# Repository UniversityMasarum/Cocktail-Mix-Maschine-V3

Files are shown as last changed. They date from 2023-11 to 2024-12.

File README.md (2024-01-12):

# Cocktail-Maschine-V3
Eine glorreiche dritte Version der Cocktailmaschine

following https://github.com/MaxVinzens/Cocktail-Mix-Maschine-V2/tree/main there now comes the better cocktail machine. To expand skills in Git, planning as well as installation and team building under the guidance of lab engineer M.Sc. Marco Braun.

# Allgemeine Hinweise / General Notes
Cocktail-Mix-Maschine-V3 ist ein Projekt an der HTWK Leipzig im Rahmen des Moduls "Ausgewählte Themen der Automatisierungstechnik" oder "Ausgewählte Themen der Elektrotechnik". 
Im Rahmen dieses Moduls wird diese Cocktailmixmaschine realisiert, die Cocktails mischen soll und die im Vergleich zu den Version V1 und V2 einige neue Features und eine erhöhte Verlässlichkeit gewährleisten soll.

# Hardware
Als feste Voraussetzung wird verlangt, dass die Kompakt-SPS X20CP1382 von der Firma B&R verwendet wird.
Die Sensor- und Aktorenauswahl ist den Studenten freigestellt, solange diese im Rahmen des Budgets sind. Eine Eismaschine soll verwendet werden!

# Software 
Als Voraussetzung für die Realisierung wurde verlangt, die Software "AutomationStudio 4.12" von der Firma B&R zu verwenden.

# Status der Entwicklung
Komponententests und Machbarkeitsstudien

# Rules 

-Please always copy the things into a parent folder 
(C code of the PLC into the PLC folder)

-Always comment on changes

-Please do not delete old things  

-please ask if you have any questions

-for research

-don't steal my cookies

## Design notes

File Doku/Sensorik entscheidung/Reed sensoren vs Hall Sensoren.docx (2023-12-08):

Reed sensoren vs Hall Sensoren

Mögliche Systeme:

System 1 Lasersensor (TOF):

Möglicher großer Messfehler
Starke Änderungen

System 2

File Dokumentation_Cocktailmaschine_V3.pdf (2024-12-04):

## FAKULTÄT INGENIEURWISSENSCHAFTEN

### E469 - AUSGEWÄHLTE THEMEN DER AUTOMATISIERUNGSTECHNIK

# Cocktailmaschine V3

Autoren | Isabel Hansen Julien Knäbel Johannes Reitmeier Philipp Schaarschmidt Niklas Scharf Andreas Wagner Simon Wagner
Betreuer | Prof. Dr.-Ing. Jens Jäkel M.Sc. Marco Braun

### 19. September 2024

### Inhaltsverzeichnis

Tabellenverzeichnis | iv
Abbildungsverzeichnis | v
1 Bedienungsanleitung | 1
2 Betrieb | 3
3 Allgemeine Konstruktion | 11
4 Stückliste | 16
5 Energieversorgung | 16
6 Module | 20

i

ii

iii

| 6.13.2 Funktion | | 99
| 6.13.3 Betrieb | | 99

### 6.13.4 Aufbau | 100

### 6.13.5 Besonderheiten | 100

7 Programmierung der SPS | 101

### 7.1 Technische Rahmenbedingungen | 101

### 7.1.1 B&R Firma generell | 101

### 7.1.2 Verwendete Hardware-Komponenten | 102

### 7.1.3 Automation Studio | 102

### 7.1.4 Strukturierter Text | 102

### 7.1.5 Netzwerkeinstellungen | 103

### 7.2 Website | 103

### 7.2.1 B&R Website generell - MappView | 103

### 7.2.2 Praktische Umsetzung der Weboberfläche | 103

### 7.3 Hauptnavigation | 104

### 7.3.1 Reinigungsprogramm | 105

### 7.3.2 Die Auswahl für den Endnutzer | 106

### 7.3.3 Der Ladebalken | 106

### 7.3.4 Eventbindings | 107

### 7.4 Code | 107

### 7.4.1 Unterprogramme | 107

### 7.4.2 Benennung der Variablen | 108

### 7.4.3 Program - Grundlegender Ablauf | 108

### 7.4.4 Program1 - Logik zum Cocktailmixen | 112

### 7.4.5 Zufall - Zufallscocktail | 115

8 Literaturverzeichnis | 120

### Tabellenverzeichnis

1 | Stückliste Pfandsystem | | 8
2 | Stückliste Rahmen | | 11
3 | Stückliste Containerhalter | | 14
4 | Stückliste Versorgung | | 17
5 | Schaltschränke | | 18
6 | Befestigungsverfahren | | 18
| iv

7 | Spannungsebenen | | 19
8 | Stückliste Förderband | | 20
9 | Pinbelegung Förderband | | 23
10 Stückliste Getränkeschlitten | | 25
11 Funktionen der Schalter | | 28
12 Stückliste Hallsensoren | | 31
13 Pinbelegung Hallsensoren | | 34
14 Stückliste Ablaufschiene | | 34
15 Stückliste Ausschankarm | | 37
16 Stückliste Endlagenschalter | | 48
17 Stückliste Schaltpanel | | 51
18 Stückliste Becherspender | | 54
19 Stückliste Becherspender Deckel | | 63
20 Stückliste Eisspender | | 71
21 Stückliste Zitronenspender | | 79
22 Stückliste Shotspender | | 87
23 Stückliste Bestelltafel | | 99

### 24 Flussraten der Schlauchpumpen | 113

### Abbildungsverzeichnis

1 | Cocktailmaschine Vorderseite | | 3
2 | Cocktailmaschine Rückseite | | 4
3 | Cocktailmaschine von rechts | | 5
4 | Cocktailmaschine von links | | 6
5 | Schaltschrank 1 | | 7
6 | Schaltschrank 2 | | 7
7 | Testgravur | | 9
8 | Lasercutter | | 9
9 | Marke | | 9
10 Rahmen aus Aluprofilen | | 12
11 Rahmen von vorne-rechts | | 12
12 Rahmen von vorne-links | | 12
13 Grundlagen für Rahmen | | 13
14 Alurohrendkappe | | 20
15 Versorgungspanel | | 21
| v

16 Datenpanel | | 21
17 D-Sub-Terminal | | 21
18 Förderband von vorne (vor Umbau) | | 22
19 Förderband von hinten (vor Umbau) | | 22
20 Förderband von vorne (nach Umbau) | | 22
21 Förderband von hinten (nach Umbau) | | 22
22 Förderbandhalterungen und -anschlüsse | | 22
23 Getränkeschlitten mit S1 und Neodym Magnet | | 24
24 Getränkeschlitten mit Wippschalter und S3 | | 24
25 Getränkeschlitten mit S2 | | 24
26 Getränkeschlitten Seitenansicht | | 24
27 Getränkeschlitten mit geöffneter Grundplatte | | 25
28 3D-gedruckte Komponenten des Getränkeschlittens | | 26
29 Position für Gewindeeinsätze und M2,5 Muttern | | 26
30 Zuordnung der Öffnungen im Getränkeschlittengehäuse | | 27
31 Grundprogramm Getränkeschlitten | | 29
32 Unterprogramm Helligkeit und Animation | | 30
33 Hallsensor | | 32
34 Hallsensor Halterung | | 32
35 Hallsensor Halterung auf Förderband | | 32
36 Hallsensor Datenpanel M12 Stecker | | 33
37 D-Sub-Terminal | | 33
38 Ablaufschiene in Förderband | | 35
39 Ablaufschiene von der Seite | | 35
40 Ablaufschiene von oben | | 35
41 Ausschankarm in Wartestellung | | 36
42 Ausschankarm in Ausgabestellung | | 36
43 Gedruckte Komponenten des Ausschankarmes | | 38
44 Schaubild Verschraubung des Ausschankarms | | 39
45 Schnittmuster des Schwammes | | 39
46 Schaltplan Licht | | 40
47 Ansicht der Platine mit ESP | | 40
48 Ansicht der Platine ohne ESP, Spannungsteiler zu erkennen | | 40
49 Animationsrichtung | | 41
50 Grundprogramm Beleuchtung | | 42
51 Unterprogramm Helligkeit und Regenbogeneffekte | | 43

vi

52 Unterprogramm Pumpenlicht und Zufallsmodus | | 45
53 Unterprogramm Polizeifarben, Warmeiß Pulsierend, Grün, Blau | | 47
54 3D-gedruckte Komponenten des Becherspendersensor | | 49
55 3D-gedruckte Komponenten des Entnahmestationssensor | | 49
56 Sensor für die Becherregistrierung aus dem Becherspender | | 50
57 Sensor für die Registrierung der Becherentnahme | | 51
58 Schaltpanel vorne | | 53
59 Schaltpanel hinten | | 53
60 Becherspender | | 56
61 verkabelte Platine | | 57
62 Rückseite Platine | | 57
63 Hilfsplatine Relais | | 57
64 Schaltplan Becher-/Eisspender | | 58
65 Grundprogramm Becher-/Eisspender | | 59
66 Unterprogramm Becherausgabe und Eisspender SPS | | 61
67 Unterprogramm Eisausgabe Becherausgabe Knopf | | 62
68 Becherspender Deckel innerer Aufbau | | 64
69 Becherspender Deckel Außen | | 64
70 Becherspender Deckel Taster | | 65
71 Becherspender Deckel offener Deckel | | 66
72 Becherspender Deckel Alarmleuchte | | 66
73 Becherspender Deckel auf Röhre | | 67
74 Grundprogramm Beleuchtung Becherspender | | 68
75 Unterprogramm Helligkeit und Modus | | 70
76 Eiswürfelmaschine EM12E | | 72
77 Eiswürfelrutsche | | 73
78 Zusammenbau-Schema Eiswürfelrutsche | | 73
79 3D-gedruckte Befestigungsplatten | | 74
80 3D-gedruckte Unterlegscheibe | | 74
81 Laserbefestigung in Laserhaltung | | 75
82 Fotozellenbefestigung in Fotozellenhalterung | | 75
83 Abgedichtetes Loch der Fotozelle | | 75
84 Steckverbindung | | 76
85 3D-gedruckte Lichtschrankenkomponenten | | 76
86 Ausgabeknopf | | 77
87 Auslösemechanismus von vorne | | 77

vii

88 Auslösemechanismus von der Seite | | 77
89 3D-gedruckte Komponenten des Auslösemechanismus | | 78
90 Aufbau der Alu-Profile | | 80
91 Schrittmotor von hinten | | 80
92 Schrittmotorkabel | | 80
93 Ansicht mit Schrittmotor | | 80
94 Halterung des Plexiglasrohres | | 81
95 Plexiglasrohr | | 81
96 Gesamtansicht | | 81
97 Platine Zitronenspender und Ausschankarm | | 82
98 Kabelanschluss | | 82
99 Kabelanschluss Tabelle | | 82
100 Schaltplan Zitronenspender und Ausschankarm | | 83
101 Gesamter Programmablaufplan | | 84
102 Unterprogramm Zitronenspender und Schalter | | 85
103 Unterprogramm Ausschankarm und Schalter | | 86
104 Anzeige- und Displayfassung | | 88
105 Anzeige- und Displayhalterung | | 88
106 Anzeigefassung | | 89
107 Arduinohalterung | | 89
108 Ausschankarm | | 90
109 Becherhaltung | | 90
110 Servohalterung | | 91
111 Servofassung | | 91
112 Pumpenhalterung | | 92
113 Aufbau des Shotspenders | | 92
114 Grundaufbau Vierquadrantensteller | | 93
115 Programmablauf Shotspender | | 94
116 Unterprogramm Bestellvorgang | | 95
117 Messwerte der Sensoren ohne Becher | | 96
118 Messwerte der Sensoren mit Bechern | | 97
119 Shotspender-Platine | | 98
120 Menü Monitor | 100
121 Rückseite Monitor | 100
122 Aufbau vorne | 100
123 Aufbau hinten | 100

viii

124 Löcher im Profil | 101
125 Hauptnavigation | 104
126 Code Passwortabfrage | 104
127 Website Reinigungsprogramm | 105
128 Website Auswahl für den Endnutzer | 106
129 Website Ladebalken | 106
130 Website Eventbindings | 107
131 Programmablaufplan Program | 109
132 Programmablaufplan Becherspender | 109
133 Programmablaufplan Eisspender | 110
134 Programmablaufplan Zitronenspender | 111
135 Programmablaufplan Cocktailmixstation | 111
136 Programmablaufplan Becherausgabe | 112
137 Code Pumpenlaufzeiten | 113
138 TOF-Übergabeparameter | 113
139 TOF-Zeitdiagramme | 113
140 Code Flankenerzeugung Anfang | 114
141 Code Flankenerzeugung Ende | 114
142 TOF Programmcode | 114
143 Code Cocktailauswertung | 114
144 Watch Cocktailauswertung | 115
145 Programmablaufplan Zufall | 116
146 Codeausschnitt Zufallsberechungen | 116
147 Programmablaufplan Zutatenbestimmung | 117
148 Programmablaufplan Mengenbestimmung | 118
149 Programmablaufplan Ergänzen der Mengen | 119
150 Programmablaufplan Prüfen der Werte | 120

ix

## 1 Bedienungsanleitung

Vorbereitung

- Vor Inbetriebnahme auf äußere Schäden überprüfen
- Monitor ausklappen

– Monitor mithilfe von M8 Schraube am Gelenk fixieren

- Auf Verunreinigungen der Getränkebehälter und Schläuche prüfen

– Falls verunreinigt: nach Anleitung im Reinigungskonzept spülen

Eiswürfelmaschine vorbereiten:

- Stöpsel in Ablauföffnung unterhalb der Maschine stecken
- Füße der Maschine auf vorgesehene Ablagepunkte platzieren
- Seitenklappe öffnen und Wasser bis zur Markierung füllen (auf Dichtigkeit achten)
- Schutzkontaktstecker in Steckdose stecken und Maschine einschalten
- Eiswürfelgröße wählen: Größe S empfehlenswert

– Produziert neun Eiswürfel in ca. sieben Minuten
– Bei Größe L verklemmen sich Eiswürfel
- Beim Befüllen und Entleeren darauf achten, dass die Maschine immer gerade steht oder gehalten wird, da sonst Wasser austritt

Becherspenderdeckel und Becherhalter einschalten (Wippschalter):

- Helligkeit einstellen (siehe Dokumentation)
- Falls notwendig 9V-Blöcke wechseln (siehe Dokumentation)
- Sollte Becherhalter in Ausgangsposition leuchten, Reset-Knopf drücken
- Becherhalter mit Wippschalter nach rechts auf Förderband platzieren

Getränkecontainer befüllen:

- Container fest in Halterungen platzieren
- Schläuche so einführen, dass diese bis in die untere Ecke reichen
- Getränke in vorgesehene Behälter schütten (siehe Beschriftungen)
- Alle Schalter am Schaltpanel ausschalten (zeigen nach unten)
- Maschine mit Stromnetz verbinden
- Becher in Becherspender füllen
- Schalter „Becherspender öffnen“ aktivieren
- Kleinen Becherstapel von unten in Becherspender schieben, sodass oberer Rand von unterem Becher knapp über dem Greifarm liegt
- Schalter „Becherspender öffnen“ deaktivieren

1

- Becher nach und nach von oben einfüllen

Schläuche befüllen:

- Auf Touchscreen Passwort „student42“ eingeben, um Reinigungsmodus freizugeben („student“ steht schon da)
- Gefäß unter Ausschankarm stellen
- Alle Pumpen mithilfe des Reinigungsprogrammes kurz anschalten, bis aus jedem Schlauch Flüssigkeit läuft
- Passwort löschen (z.B. nur die „42“) um Reinigungsmodus zu deaktivieren

Laptop mit Bildschirm verbinden, um Menü anzuzeigen.

Betrieb

- Bestellung über Touchscreen
- Auswahl zwischen alkoholischen Getränken oder Softdrinks
- Ausgabeprozess vollautomatisch
- Getränk erst entnehmen, wenn Becher am rechten Ende angekommen ist

Funktion Schaltpanel:

- Notstop: friert Förderband und Pumpen ein
- Licht EIN / AUS: Beleuchtung der Getränkecontainer aktivieren/deaktivieren
- Modi der Beleuchtung:

– Position 1: Regenbogeneffekt
– Position 2: Pumpenlicht (aktive Pumpen beleuchtet) – Position 3: Zufallsmodus
– Position 4: Blau-Rot-Beleuchtung
– Position 5: Warmweiß pulsierend
– Position 6: Licht Grün
– Position 7: Licht Blau
- Helligkeit: in 10%-Schritten einstellbar
- Becherspender öffnen: öffnet Greifarme zum Beladen/Entladen
- Eisausgabe 1x drücken: Eisausgabezyklus
- 1x Becher: gibt einen Becher aus
- Zitronenspender EIN / AUS: aktiviert Zitronenspender
- Ausschankarm hoch / runter: Position des Arms bestimmen
- Shotspender Stromversorgung: ein/aus schalten

Becher nachfüllen:

- Wenn Rundumleuchte am Becherspender angeht

2

- Nicht überfüllen (Überlastung des Becherspenders vermeiden)

Eis nachfüllen:

- Eis in obere Klappe der Eismaschine nachfüllen
- Eismaschine kann vorher eingeschaltet werden, Eiswürfel in Gefrierbeuteln lagern

Nach der Verwendung

- Reinigung gemäß Reinigungskonzept
- Maschine von Strom trennen

## 2 Betrieb

### 2.1 Übersicht

Abbildung 1: Cocktailmaschine Vorderseite

3

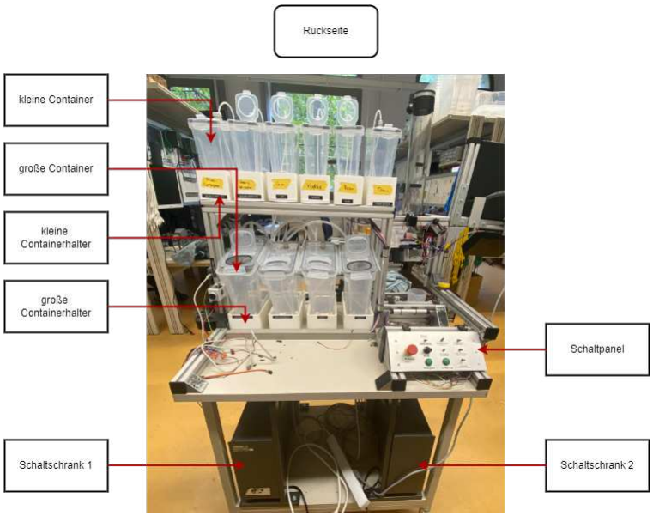
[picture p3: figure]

Abbildung 2: Cocktailmaschine Rückseite

4

Abbildung 3: Cocktailmaschine von rechts

5

Abbildung 4: Cocktailmaschine von links

6

Abbildung 5: Schaltschrank 1

Abbildung 6: Schaltschrank 2

### 2.2 Reinigungskonzept

Diese Reinigungsschritte sollen nach jeder Nutzung durchgeführt werden.

Getränkebehälter

1. Getränke aus den Behältern entfernen.
2. Topf unter Ausschankarm stellen und leeren, wenn er zu voll wird.

7

3. Mit kaltem Wasser Schläuche durchpumpen.
4. Warmes Wasser mit Spülmittel nachfüllen und Schläuche durchpumpen.
5. Danach klares Wasser hinzugeben, um restliche Spülmittelreste aus den Schläuchen zu entfernen.
6. Behälter trocknen lassen (unverschlossen).

Nach längerer Nichtnutzung der Maschine die Schläuche entfernen und reinigen.

Eismaschine

1. Restliches Wasser und Eis entfernen.
2. Eismaschine reinigen.

Zitronenspender

1. Plexiglasplatte abschrauben sowie das Plexiglasrohr aus der Halterung entnehmen.
2. Alle Plexiglasplatten sowie das Plexiglasrohr mit Spülmittel und warmem Wasser reinigen.
3. Bauteile abtrocknen.

Sonstiges

- Ablaufrinne und den Auffangbehälter leeren und reinigen.
- Förderband reinigen, falls notwendig.
- Becherhalterung reinigen, falls notwendig.

### 2.3 Pfandsystem

### 2.3.1 Stückliste

Bauteil | Anzahl
Furnier Pappel Platten 30,5x36,5cm (ges. 0,445m²) | 4

Tabelle 1: Stückliste Pfandsystem

### 2.3.2 Funktion

- Pfandmarken für Becher

### 2.3.3 Betrieb

- Bei Kauf eines Cocktails erhält Kunde zusätzlich eine Pfandmarke
- Bei Abgabe von Marke und Becher erhält der Kunde den, durch den Pfand entstandenen Aufpreis zurück

8

### 2.3.4 Aufbau

- Größe der Platten abgestimmt auf maximale Fläche des im Labor vorhandenen Lasercutters
- Logo zunächst auf die Vorderseite der Platten eingebrannt
- Platten umgedreht, Wert der Marke eingebrannt sowie ausgeschnitten

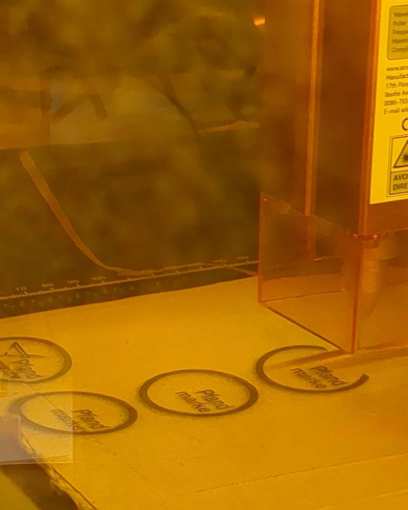
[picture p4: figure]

Abbildung 7: Testgravur

Abbildung 8: Lasercutter

### 2.3.5 Besonderheiten

Design

- Vorderseite mit Logo graviert (Oktopus)
- Rückseite spiegelt Wert der Marke wieder (zwei Euro)

Abbildung 9: Marke

9

Preisanpassung

- Preis für einen Cocktail auf drei Euro gesetzt
- Pfandmarke (zwei Euro) erhöht Gesamtpreis auf fünf Euro
- Getränk leicht mit einem Schein zu bezahlen

StuRa-Pfandsystem

- Marken bisher nicht genutzt
- Nur Veranstaltungen von Studentischer Selbstverwaltung (StuRa, FSR) begleitet
- Hier ist bereits Pfandsystem integriert, hat bisher ausreichend funktioniert

10

## 3 Allgemeine Konstruktion

### 3.1 Rahmen- und Stützstrukturen

### 3.1.1 Stückliste

Bauteil (Nutenprofil Aluminium, M8 Nut) | | Menge
Größe Querschnitt [mm] | Länge [mm] | | Bezeichnung
40x40 | 70 | 1 | Halterung Endlagenschalter
40x40 | 93 | 1 | Becherspender Längshalterung unten
40x40 | 110 | 1 | Querstrebe Eisrutsche
40x40 | 145 | 3 | Längsstreben oben
40x40 | 170 | 1 | Zitronenspender quer unten
40x40 | 200 | 1 | Zitronenspender längs oben
40x40 | 225 | 1 | Becherspender Längshalterung oben
40x40 | 230 | 1 | Zitronenspender längs unten
40x40 | 250 | 1 | Becherspender Hochkantstütze
40x40 | 295 | 1 | Querstrebe Eisservo
40x40 | 310 | 1 | Stütze Monitor hochkant
40x40 | 390 | 1 | Querstrebe Monitor
40x40 | 410 | 4 | Stützen hochkant
40x40 | 560 | 1 | Querstrebe unten
40x40 | 590 | 3 | Fundament längs auf Tisch
40x40 | 640 | 2 | Querstreben oben
40x40 | 690 | 1 | Längsstrebe Umrandung Eismaschine
40x80 | 295 | 1 | Eismaschine Fundament quer vorne
40x80 | 335 | 1 | Eismaschine Fundament quer hinten
Aluminium Profilwinkel 40x40 | | 37
Aluminium Profilwinkel 80x80 | | 6
Profilabdeckkappen 40x40 | | 15
Profilabdeckkappen 40x120 | | 3
Winkelabdeckkappen 40x40 | | 37
Winkelabdeckkappen 80x80 | | 6

Tabelle 2: Stückliste Rahmen

### 3.1.2 Funktion

Dient als generelle Struktur und Halterung vieler Baugruppen.

11

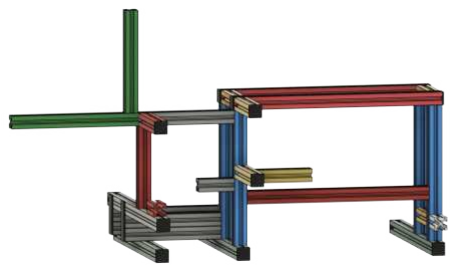
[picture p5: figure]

Abbildung 10: Rahmen aus Aluprofilen

### 3.1.3 Aufbau

- Drei Längsprofile auf Tisch montiert

– Fundament des restlichen Aufbaus
– Sehr stabile Bauteile
– Einfache aber effektive und flexible Montage durch Schraubverbindungen, Nutensteine und Profilwinkel
- Benötigt wurden Halterungen für:

– Pumpen und Schläuche
– Kleine Flüssigkeitscontainer – Ausschankarm
– Zitronenspender
– Eisrutsche
– Eismaschine
– Becherspender
– Monitor und Bestellpanel – Controlpanel
– Shotspender
– Endlagenschalter
– Kabelführungen
Abbildung 11: Rahmen von vorne-rechts | Abbildung 12: Rahmen von vorne-links

12

### 3.1.4 Besonderheiten

- Flexibles System:

– Kann wieder auseinandergebaut werden
– Leicht zu erweitern
– Mit Hilfe von 3D-Druck auf jedes Modul anpassbar

Abbildung 13: Grundlagen für Rahmen

13

### 3.2 Containerhalter

### 3.2.1 Stückliste

Bauteil | Anzahl
Großer Containerhalter | 4
Kleiner Containerhalter | 6
Plexiglasplatte 245x98x5 mm | 4
Plexiglasplatte 195x80x5 mm | 6
M8x50 Maschinenbauschrauben | 12
M8 Unterlegscheiben | 24
M8 Federringe | 12
M6x16 Maschinenbauschrauben | 24
M6 Nutensteine | 24
Kleine Peristaltikpumpe | 6
Große Peristaltikpumpe | 4
M2,5x16 Maschinenbauschraube | 12
M2,5 Mutter | 12
M3x20 Maschinenbauschrauben | 16
M3 Unterlegscheiben | 16
M3 Federringe | 16
M3 Muttern | 16
300 Ohm Resistor | 6
680 Ohm Resistor | 4
Weiße LED | 10
Lichtblende kleine Schlauchpumpe | 6
Lichtblende große Schlauchpumpe | 4

Tabelle 3: Stückliste Containerhalter

### 3.2.2 Funktion

Sowohl die großen als auch kleinen Containerhalter erfüllen die gleichen Funktionen. Mithilfe dieser lassen sich die Container fest an der Maschine montieren. Die Container werden in Schräglage befestigt, damit sämtliche Flüssigkeiten an einem Ende zusammenlaufen und vollständig herausgepumpt werden können. Durch die Schräge können die Peristaltikpumpen unterhalb der Container mithilfe des gleichen Druckes montiert werden. Zudem können LED-Panel unterhalb der Container befestigt werden, um die Getränke zu beleuchten. Am unteren Ende der Aussparung für die Pumpenmotoren befinden sich kleine Vertiefungen, durch welche LEDs durchgeführt werden können, um die Pumpen beleuchten zu können.

14

Druckanweisungen

- Kein Unterstützungsmaterial notwendig.
- Niedrige Fülldichte verwenden.
- Auf gute Bodenhaftung achten, um Verformungen zu vermeiden.
- PLA eignet sich besonders gut aufgrund guter Druckeigenschaften bei großen Drucken.

### 3.2.3 Besonderheiten

großer Containerhalter

- Bauteil zu groß für die meisten 3D-Drucker.

– Druck in zwei Teilen.

- Verkleben beider Teile nach Druck.

– UHU Hart Kunststoff gut geeignet.
– Zu flüssige Klebstoffe ziehen in Poren von 3D-Druck ein. – Beachten, dass einige Klebstoffe PLA auflösen können.

kleiner Containerhalter

- Klein genug, um auf Ender 3 in einem Stück gedruckt zu werden.

– Im Labor vorhandener Bambulab X1 Carbon könnte Probleme haben, da Kalibrierungslinien im Weg sein könnten.
– In diesem Fall Bauteil halbieren.

### 3.2.4 Montage

- Große Container mit M8 Maschinenbauschrauben an der Tischplatte verschrauben.

– Möglichst große Unterlegscheiben verwenden, um Krafteinwirkungen zu verteilen.
– Schrauben nicht zu fest anziehen.
- Kleine Containerhalter mit M6 Maschinenbauschrauben in M6 Nutensteinen im Aluprofil verschrauben.
- Kleine Peristaltikpumpen mit M2,5 Maschinenbauschrauben in kleinen Containerhaltern verschrauben.
- Große Peristaltikpumpen mit M3 Maschinenbauschrauben in großen Containerhaltern verschrauben.
- Weiße LEDs parallel zu den Pumpen schalten.

– Bei kleinen Containerhaltern LEDs 300 Ohm Widerstand vorschalten.
– Bei großen Containerhaltern LEDs 680 Ohm Widerstand vorschalten. – Siehe Stromlaufplan.
- Lichtblenden für kleine und große Pumpen anbringen.

– Bei großen Pumpen werden Blenden nur festgeklebt.

15

– Bei kleinen Pumpen müssen die unteren zwei Schrauben, welche die Glasabdeckung befestigen, entfernt und mit längeren ersetzt werden.

- Kleine Container an der langen Seite des oberen Randes mit Schaumstoffstreifen bekleben, um Container zu stabilisieren.

– Schaumstoffstreifen nicht über die gesamte Länge der oberen Kante ziehen, damit Plexiglasplatten noch eingeschoben werden können.

- Plexiglasscheiben schützen die darunter liegende Elektronik vor überlaufenden Flüssigkeiten.

## 4 Stückliste

Die Stückliste der Cocktailmaschine V3 ist aus dem folgenden Link zu entnehmen.

https://github.com/UniversityMasarum/Cocktail-Mix-Maschine-V3/blob/master/Cocktailmaschine_V3_Stückliste.pdf

## 5 Energieversorgung

Die Energieversorgung der Cocktailmaschine muss robust gegen äußere Einflüsse, optisch ansprechend und vor allem sicher für den Anwender sein. Dazu kommt noch eine möglichst schnelle und verfügbare Art und Weise des Anschlusses an Energiequellen zu gewährleisten.

16

### 5.1 Stückliste

Bauteil | Anzahl
Sperrholzplatten | 2
Siemens Schaltschrank 32x48x10cm | 2
Plexiglasscheiben Breite=45cm, Höhe=29,5 | 2
Hutschiene ca. 40cm | 2
WAGO 221-2411 Durchgangsverbinder max. 4 mm², 2 Leiter | 8
WAGO 221-412 Verbindungsklemme, 2-Leiteranschluss | 8
WAGO 221-413 Verbindungsklemme, 3-Leiteranschluss | 24
WAGO 221-415 Verbindungsklemme, 5-Leiteranschluss | 25
Befestigungsadapter WAGO 221-500 (Hutschienenadapter) | 4
UT 4 GR Universal-Terminal 0,14-4mm², grau (Reinklemme) | 1
UT 6 BL Universal-Terminal 0,2-6mm², blau (Reinklemme) | 1
UT 4 PE Universal-Terminal 0,14-4mm², grün/gelb (Reinklemme) | 1
Installationskanal CK 30x30 PVC lichtgrau ca. 60cm | 1
Verdrahtungskanal mit Deckel 25x37,5mm, 1m | 3
Verdrahtungskanal 10mm | Länge: 50cm
Alurohr Durchmesser 20mm, Wandstärke 2mm, ca.1,5m | 1
Alurohrendkappen (3D gedruckt) | 8
Kabelhalter Nut 8 | 20
Aderendhülsen 0,5mm², 1mm², 1,5mm², 2,5mm² | 70
Kabelverschraubung M20 | 1
Schutzkontaktstecker mit Kabel NYY-J 3x1,5mm², Länge: 1,8m | 1
LiYv, 0,5 mm², 25 m, rot | 1
LiYv, 0,5 mm², 25 m, blau | 1
LiYv, 0,5 mm², 25 m, grün | 1
LiYv, 0,5 mm², 25 m, violett | 1
LiYv, 0,5 mm², 25 m, orange | 1
LiYv, 0,5 mm², 25 m, weiß | 1
Cat.7 Netzwerkkabel1000 MHz S/FTP PIMF orange, ca. 8m | 1
H05V-K, 1,0 mm², blau, ca. 6m | 1
H05V-K, 1,0 mm², rot, ca. 22m | 1
H07V-K 1,5 mm² blau ca.15m | 1
H07V-K 1x1,5 grün/gelb Ring, ca. 5m | 1
H07V-K 1,5mm² grau, ca. 1,5m | 1
H07V-K 1,5 mm² orange, ca. 14m | 1
H07V-U 1x2,5 mm² violett, ca. 11m | 1
H07V-U 2,5 mm² grün/gelb ca. 0,20cm | 1
5V-Netzteil: Phoenix Contact | 1
24V-Netzteil: Phoenix Contact | 1
12V-Netzteil: omron S82K-03012 | 1

Tabelle 4: Stückliste Versorgung

### 5.2 Aufbau des Versorgungssystems

Vorbereitung für die Verkabelung der Cocktailmaschine und Schaltschränke

- Schaltschränke auf der unteren Auflagefläche montieren (z.B. Löcher in Fußgestell bohren und mit Holzschrauben fixieren)
- Kabelverschraubung in Loch im Boden des Schrank 1 anbringen
- Holzplatten zurechtschneiden und Bereich für den Schutzleiteranschluss am Schrankgehäuse

17 aussägen, anschließend mit M5 Maschinenschrauben und großen Unterlegscheiben anschrauben

- Eine Hutschiene in beide Schränke mittels Holzschrauben anbringen

Aufteilung der Komponenten in den Schränken

Schaltschrank 1 | Schaltschrank 2
Aufrasten auf Hutschiene: - Reihenklemme: Phase, Neutralleiter und Schutzleiter - WAGO-Befestigungsadapter - 5V-Netzteil - 12V-Netzteil - 24V-Netzteil Ankleben mit doppelseitigem Klebeband: - Verdrahtungskanal rechts | Aufrasten auf Hutschiene: - SPS - 2x WAGO-Befestigungsadapter - 14x Koppelrelais Ankleben mit doppelseitigem Klebeband: - Platine für Becher- und Eisspender - Platine für Zitronenspender und Ausschankarm - Beleuchtungssteuerungsplatine - Shotspendersteuerungsplatine - Verdrahtungskanal unten, rechts und oben - 3x 5er WAGO-Verbindungsklemme

Tabelle 5: Schaltschränke

- Installationskanal zusägen und auf der Oberseite der oberen Platte, hinter den unteren Getränkehaltern anschrauben.
- Verdrahtungskanal so an Unterseite der oberen Platte und an den Schränken mit doppelseitigem Klebeband fixieren, dass eine durchgehende Kanalstrecke entsteht.
- Kleiner Verdrahtungskanal hinter Aluprofil der oberen Getränkehalter kleben.
- Für Kabelverlegung entlang der Alu-Profile Alurohr mit Endkappen mittels Kabelbinder an Kabelhalter befestigen (Endkappen können 3D gedruckt werden).
- WAGO-Verbindungsklemmen mittels doppelseitigem Klebeband an Unterseite der oberen Platte für Abzweigungen vorbereiten.

Anschluss der Kabel und Verlegung

Für den Anschluss der Leiterenden, an einen Kontakt, müssen diese vom Isoliermaterial befreit werden.

Befestigungsverfahren | Hinweis
Direktes Löten | Verbindung durch Aufschmelzen von Lötzinn unter Verwendung von Flussmittel und anschließendes Erstarren (falls nötig, anschließend Schrumpfschlauch zur Isolation darüber ziehen und erwärmen)
Schraubklemme | auf abisoliertes Ende eine Aderendhülse pressen (auch bei Eingängen der SPS nötig)
WAGO-Verbindungsklemme | abisoliertes Ende wird in Klemme eingeführt

Tabelle 6: Befestigungsverfahren

18

- Stromversorgung der Maschine erfolgt über einen Schutzkontaktstecker, der in eine herkömmliche Schuko-Steckdose (230 V, Typ F) eingesteckt wird (Die Eismaschine und der Monitor für die Getränkekarte müssen separat über einen Schukostecker an eine Schukosteckdose des Typs F angeschlossen werden).
- Kabel des Schuko-Steckers durch die Unterseite in den Schrank 1 führen, dort mittels Kabelverschraubung zugentlasten und an die Reihenklemmen für Phase, Neutralleiter und Schutzleiter anschließen.
- Von Reihenklemmen mittels H07V-K Brücken zu WAGO-Klemmen und anschließend zu den 5V-, 12V- und 24V-Netzteilen.
- Grün-gelber Schutzleiter mit dem Gehäuse von Schrank 1 und Schrank 2 sowie mit dem WAGO-Switch 852-111 und dem Förderband verbinden.

Spannungsebenen und die dazugehörigen Verbraucher

5V | 12V | 24V
- Platine für Becher- und Eisspender | - kleine Peristaltikpumpen und | - speicherprogrammierbare Steuerung
- Platine für Zitronenspender | parallel geschaltene Widerstände | - große Peristaltikpumpen und parallel
und Ausschankarm | und Leuchtdioden | geschaltene Widerstände und Leuchtdioden
- Beleuchtungssteuerungsplatine | - Schrittmotor des Zitronen- | - WAGO-Switch 852-111
- Shotspendersteuerungsplatine | spenders | - B&R Touchscreen
- Servomotoren in Becherspender,
Eisspender, Ausschankarm und
Shotspender
- fokussierbares Lasermodul
- Beleuchtung der Getränke und der Shotgläser

Tabelle 7: Spannungsebenen

Hinweis: Der Maximalbetrieb der RGB-LED-Panels für die Getränkebehälter ist nicht möglich, da dies das 5V-Netzteil überlasten würde. Um dies zu verhindern, werden Helligkeitsanpassungen und geeignete Lichteffekte eingesetzt, bei denen nicht immer alle Leuchtdioden gleichzeitig weißes Licht abstrahlen. Dies wird softwaretechnisch realisiert.

Die Masse der 5-V-Spannungsebene ist separat zur zusammengefassten Masse der 12-V- und 24-V-Spannungsebene geführt, um „zitternde“ Servomotoren und flackernde Lichter zu vermeiden.

- Weitere Informationen zur Verkabelung können dem Stromlaufplan entnommen werden.

Auswahl des Leiterquerschnittes:

- Querschnitt der Kupferleiter für die Komponentenversorgung beträgt mindestens 1 mm² und ist damit mit bis zu 15 A belastbar (Die höchste Stromstärke im Normalbetrieb wird mit 6,5 A in der Versorgungsleitung der Getränkebehälterbeleuchtung erwartet).
- Signalübertragungsverbindungen haben einen Leiterquerschnitt von 0,5 mm² oder bestehen aus Aderpaaren eines CAT-7-Netzwerkkabels, das durch geerdete Schirmung eine störungsfreie Signalübertragung ermöglicht.

19

Schutzvorrichtungen:

- Alle selbst entwickelten Module der Cocktailmaschine arbeiten mit Sicherheitskleinspannung
- Zum Schutz vor Berührung, Fremdkörpern und Flüssigkeiten sind die Schränke durch angeschraubte Plexiglasscheiben abgeschirmt
- Kabelkanäle und Alurohre schützen die Kabel

Informationen zu der Alurohrendkappe:

- Material: PLA
- Kein Unterstützungsmaterial nötig
- Nutzen: Schützt Leiter vor scharfen Kanten am Alurohr

Abbildung 14: Alurohrendkappe

## 6 Module

### 6.1 Förderband

### 6.1.1 Stückliste

Bauteil | Anzahl
Transfersystem 24V DC | 1
D-Sub 25-Kabel | 1
Bananenstecker | 3

Tabelle 8: Stückliste Förderband

### 6.1.2 Funktion

- Transfer des Bechers zwischen den einzelnen Stationen

20

### 6.1.3 Betrieb

- Motor innerhalb des Förderbandes ist über Achse mit zwei Bändern verbunden
- Im Betrieb benötigt Motor 24V / 1,1A
- Drehrichtung kann über entsprechende Pin-Ansteuerung geändert werden

### 6.1.4 Aufbau

- Am Rahmen sind zwei Panele angebracht

– Versorgungspanel mit Bananenbuchsen
– Datenpanel mit acht M12-Buchsen und einer D-Sub 25-Buchse
Abbildung 15: Versorgungspanel | Abbildung 16: Datenpanel
- Pinbelegung von Datenpanel und Versorgungspanel intern verschalten
- Nach ausgiebiger Durchgangsprüfung Pinbelegung festgestellt
- Möglichkeit des Austausches zwischen Links- und Rechtslauf des Förderbandes sowie sechs externer Geräte und SPS über D-Sub 25-Anschluss

Abbildung 17: D-Sub-Terminal

21

- Anschluss der Betriebsspannung mit 24V, Masse und PE über Bananenstecker am Versorgungspanel
- Für Nutzung der Richtungssteuerung per D-Sub 25-Anschluss muss der Schalter “SPEED CTRL. INT.” auf INT. (intern) gestellt werden

Abbildung 18: Förderband von vorne (vor Umbau)

Abbildung 19: Förderband von hinten (vor Umbau)

### 6.1.5 Besonderheiten

Umbau Förderband

- Förderband besitzt zwei Panele (Versorgungspanel, Datenpanel)
- Jeweils eines der beiden auf einer Seite
- Umbau so, dass beide Panele auf einer Seite sind
- Vorteile:
– Unbefugte Personen kommen nicht an Schaltungen
– Schaltung nicht von außen zu sehen
– Kürzere und unumständlichere Verkabelung zwischen Förderband, Sensorik und SPS

Abbildung 20: Förderband von vorne (nach Umbau)

Abbildung 21: Förderband von hinten (nach Umbau)

Halterung

- Sechs kleine Halterungen an Tischplatte unter Förderband angeschraubt
- Füße des Förderbandes können dort hineingestellt werden
- Kein Verrutschen des Förderbandes möglich

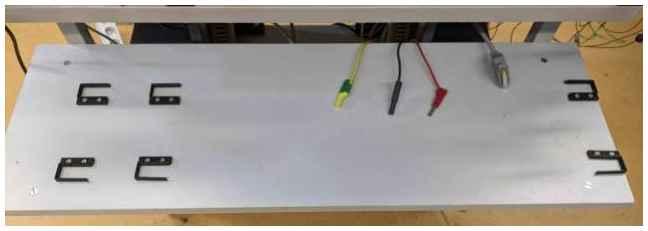
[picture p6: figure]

Abbildung 22: Förderbandhalterungen und -anschlüsse

22

Pinbelegung

D-Sub 25 Pin | M12 Pin | Bezeichnung/Belegung
1 | X5 1.4 | nicht verwendet
2 | X5 2.1 | nicht verwendet
3 | X5 3.4 | nicht verwendet
4 | X5 4.1 | nicht verwendet
5 | X5 5.4 | nicht verwendet
6 | X5 6.1 | nicht verwendet
7 | X5 7.4 | Band Rechtslauf
8 | X5 8.1 | Band Linkslauf
9 | - | nicht verwendet
10 | X5 1.1 / 2.2 / 3.1 / 4.2 / 5.1 / 6.2 / 7.1 / 8.2 | Spannungsversorgung 24V
11 | - | keine interne Verschaltung
12 | - | keine interne Verschaltung
13 | X5 1.3 / 2.4 / 3.3 / 4.4 / 5.3 / 6.4 / 7.3 / 8.4 | Masse 1
14 | X5 1.2 | Datenpin Hallsensor 1
15 | X5 2.3 | Datenpin Hallsensor 2
16 | X5 3.2 | Datenpin Hallsensor 3
17 | X5 4.3 | Datenpin Hallsensor 4
18 | X5 5.2 | Datenpin Hallsensor 5
19 | X5 6.3 | nicht verwendet
20 | X5 7.2 | Reserve Band Linkslauf
21 | X5 8.3 | Reserve Band Linkslauf
22 | - | nicht verwendet
23 | X5 1.1 / 2.2 / 3.1 / 4.2 / 5.1 / 6.2 / 7.1 / 8.2 | Intern mit Pin 10 gebrückt
24 | - | nicht verwendet
25 | X5 1.3 / 2.4 / 3.3 / 4.4 / 5.3 / 6.4 / 7.3 / 8.4 | Masse 2

Tabelle 9: Pinbelegung Förderband

### 6.2 Getränkeschlitten

Der Getränkeschlitten hat die Aufgabe einen Becher zuverlässig aus dem Becherspender aufzunehmen, diesen sicher zu den einzelnen Stationen entlang des Förderbandes zu transportieren und eine leichte Entnahme durch den Kunden zu ermöglichen. Ebenso soll der Getränkeschlitten entlang des Förderbandes für die SPS lokalisierbar sein und selbst den Fortschritt der Cocktailherstellung registrieren.

23

Abbildung 23: Getränkeschlitten mit S1 und Neodym Magnet

Abbildung 24: Getränkeschlitten mit Wippschalter und S3

Abbildung 25: Getränkeschlitten mit S2 | Abbildung 26: Getränkeschlitten Seitenansicht

24

Abbildung 27: Getränkeschlitten mit geöffneter Grundplatte

### 6.2.1 Stückliste

Bauteil | Anzahl
Neodym Magnet (D=7mm/ Höhe=3mm) | 1
Mikro Rollhebelschalter | 1
Wippschalter 1802 | 1
Kurzhubtaster | 2
Plexiglasscheibe (Durchmesser=60mm/ Höhe=3mm) | 1
Arduino Nano | 1
LED-Ring RGB WS2812B | 1
Lochplatine (Länge=70mm/ Breite=20mm) | 1
Widerstand R= 10kΩ | 3
9V Block | 1
9V Block Batterieclip | 1
M3x6 Maschinenschrauben | 4
M3x12 Maschinenschrauben + Unterlegscheibe | 4
M3x5,7 Gewindeeinsatz | 8
M2,5x10 Maschinenschrauben + Unterlegscheibe | 2
M2,5 Mutter | 2
LiYv 1x0,5mm² blau (ca. 50cm) | 1
LiYv 1x0,5mm² rot (ca. 50cm) | 1
LiYv 1x0,5mm² orange (ca. 10cm) | 1
Buchsenleiste (15 Buchsen) | 2

Tabelle 10: Stückliste Getränkeschlitten

### 6.2.2 Druckanweisung

- mit Unterstützungsmaterial
- keine hohe Fülldichte nötig
- Material: PLA

25

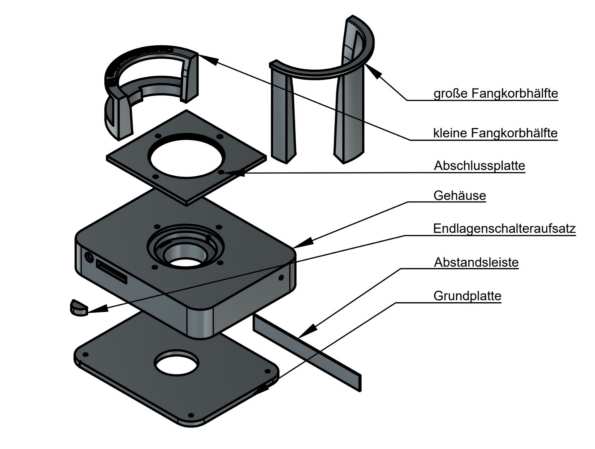
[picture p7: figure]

Abbildung 28: 3D-gedruckte Komponenten des Getränkeschlittens

### 6.2.3 Zusammenbau der einzelnen Komponenten

- 3D gedruckte Teile vom Unterstützungsmaterial befreien

Abbildung 29: Position für Gewindeeinsätze und M2,5 Muttern

- Gewindeeinsätze mittels Gasbrenner erhitzen und mit einer geeigneten Zange in die angegebenen Löcher drücken (schmelzen)
- M2,5 Mutter mit einem stumpfen Gegenstand (Holzstiel eines Hammers) in die Vertiefung pressen
- an Taster- und Wippschalterkontakte Leiter (LiYv) löten, anschließend in vorgesehene Öffnungen schieben und mit Heißkleber von innen fixieren
- Leiter an Rollhebelschalter anlöten (wird als Schließer verwendet)

26

- Endlagenschalteraufsatz auf Schalterarm drücken und mit Sekundenkleber sichern (dieser ermöglicht die beidseitige Betätigung beim Links- und Rechtslauf des Förderbandes)
- Rollhebelschalter mittels M2,5x10 Maschinenschrauben und Unterlegscheiben fixieren

Abbildung 30: Zuordnung der Öffnungen im Getränkeschlittengehäuse

- Neodym Magnet mit einem stumpfen Gegenstand in Öffnung pressen
- LED-Ring von Oberseite so einschieben, dass Kontakte durch die Anschlussöffnung frei zugänglich sind und Leiter anlöten
- auf Lochplatine Buchsenleisten in Passgröße des Arduino Nano, sowie 10kΩ- Pulldown-Widerstände anlöten
- 9V Block Batterieclip, sowie Leiter der Schalter und Taster an Platine anlöten und nach Schaltplan verschalten (siehe „Schaltplan_Becherhalter“) Hinweis: vor Inbetriebnahme Leiterbahnen auf der Platine durchmessen, um Kurschlüsse zu vermeiden
- Programm „Becherhalterbeleuchtung“ auf Arduino laden
- 9V Block in Käfig einschieben und mit Batterieclip verbinden
- Plexiglasscheibe über den LED-Ring einlegen, darüber die Abschlussplatte so positionieren, dass von der Unterseite des Gehäuses, die M3x12 Schrauben, mit Unterlegscheibe, durch die Löcher gefädelt und mit den Fangkorbhälften verschraubt werden kann (dabei werden Abschlussplatte und Plexiglasscheibe verklemmt und fixiert)
- Für Feuchtigkeitsschutz alle Kanten auf der Gehäuseoberseite mittels Heißklebernaht abdichten
- Grundplatte mittels M3x6 Maschinenschrauben mit Gehäuse verschrauben

### 6.2.4 Allgemeine Erläuterung

Positionsübermittlung des Becherhalters an die SPS

Entlang des Förderbandes befinden sich Hallsensoren, welche das vom verbauten Neodym Magneten erzeugte Magnetfeld registrieren und ein Signal an die SPS schicken.

Positionserkennung des Becherhalters

Beim Vorbeifahren des Becherhalters an den Hallsensoren wird der Endlagenschalter betätigt. Jede Betätigung wird vom Arduino erfasst und gezählt, sodass passend zur Station ein Lichteffekt wiedergegeben werden kann. Nachdem der Becherspender an der Getränkeausgabe angekommen ist, wird

27 das Licht auf dem Rückweg ausgeschaltet. Dies verlängert die Lebensdauer der Batterie. Weitere Informationen können dem Programmablaufplan entnommen werden.

Hinweis: Der Becherhalter muss an der Ausgangsposition, an dem Becherspender eingeschalten, oder zurückgesetzt werden. Andernfalls kommen nicht die gewünschten Lichtanimationen an den jeweiligen Stationen.

Batterielaufzeit

Der maximale Strombedarf der Schaltung liegt bei 46mA (Helligkeitseinstellung → alle LEDs sind weiß).

Batterielaufzeit bei einem 9V-Block mit 640mAh*:

Batterielaufzeit t = Kapazität 9V-Block / max. Strombedarf = 640mAh/46mA = 13,9h

Im Ruhemodus hat die Schaltung einen Strombedarf von 21 mA. (Diese Werte wurden messtechnisch mit einem Digital-Multimeter VC-125 ermittelt.)
Der Wippschalter unterbricht den Stromkreis zur Batterie. Dies verhindert eine schnelle Entladung der
Batterie bei Nichtnutzung.

*https://www.varta-ag.com/fileadmin/varta/industry/images/products/Industrial_Pro/VM_Folder_Industrial_Pro_2023_Web.pdf

Hinweis zum Stromlaufplan

Schaltobjekt | Pin | Funktion
Rollhebelschalter (S1) | D03 | Stationserkennung
Taster (S2) | D03 | Zurücksetzen
Taster (S3) neben dem Wippschalter | D04 | Helligkeitseinstellung

Tabelle 11: Funktionen der Schalter

### 6.2.5 Programmablauf

Grundprogramm

- LEDs ausschalten, um vorherige Zustände zu löschen
- Auf Inputs warten

– Knopf „Helligkeit“ gedrückt
– Taster „Station“ betätigt
– Knopf „Reset“ gedrückt

Taster „Station“ betätigt

- Dieser Taster befindet sich an der Seite des Becherhalters und wird während der Fahrt betätigt, indem dieser gegen die Hallsensoren drückt

– Becherhalter kennt die Station, an der er sich befindet

- Variable counterStation zählt mit, an welcher Station der Becherhalter sich befindet

– Hin und zurück sind 7 Klicks

- Aktionen bei Werten von counterStation:

28

– 1: LEDs aus → Startposition, es wird Energie gespart, wenn Becherhalter nicht in Benutzung
– 2: LED Animation Blau
– 3: LED Animation Gelb
– 4: LED Animation Magenta
– 5 – 7: LED Animation Rot (Becherhalter ist auf dem Rückweg), wenn an Startposition angekommen, counterStation = 1 → LEDs aus

Knopf „Reset“ gedrückt

- Setzt Variable counterStation auf 1, um Programm von vorne beginnen zu lassen

Abbildung 31: Grundprogramm Getränkeschlitten

Unterprogramm Animation

- for-Schleife von i = 0 bis i < 12 laufen lassen

– LED(i) auf Farbe der Station schalten
– Pause von Animationsdauer / 12 (Anzahl LEDs auf LED-Ring)

29

Unterprogramm Helligkeit

- Variable count zählt die Anzahl der Tastendrücke
- 6 Helligkeitsstufen

– Helligkeit berechnet mit Formel: Helligkeit = 255 / 6 * count

- LED-Ring füllt sich mit zunehmender Helligkeit

– Berechnet mit Formel: LEDs an = 2 * count

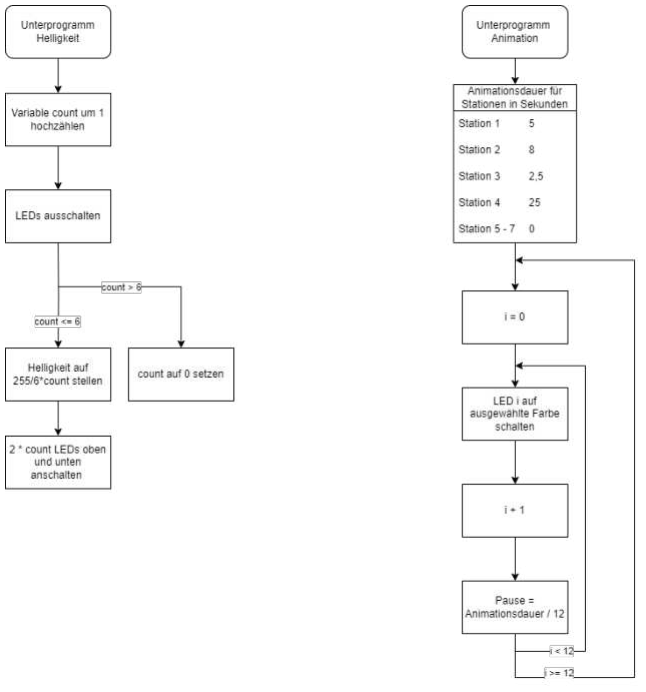
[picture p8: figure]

Abbildung 32: Unterprogramm Helligkeit und Animation

30

### 6.3 Hallsensoren

### 6.3.1 Stückliste

Bauteil | Anzahl
Hallsensor | 5
Halterung Hallsensor | 5
M12 Stecker gewinkelt | 5
D-Sub 25 Terminalblock | 1
Aderendhülsen 0,5 mm² | 15
M3x25 Maschinenbauschraube | 10
M3x10 Maschinenbauschraube | 6
M3 Unterlegscheibe | 14
M3 Mutter | 10
M3 Nutenstein | 6
M4x10 Maschinenbauschraube | 4
M4 Unterlegscheibe | 4
M4 Nutenstein | 4
Kabelkanal | 50cm

Tabelle 12: Stückliste Hallsensoren

### 6.3.2 Funktion

Feststellung der Position des Schlittens und Festlegung der Stationen.

### 6.3.3 Betrieb

- Sensorkopf detektiert Magnetfelder in kleinem Bereich vor ihm
- Im Betrieb benötigt der Sensor 24V / 0,2A
- Schlitten für Transport des Bechers beinhaltet im Gehäuse einen kleinen Neodym Magneten

– Sensor erkennt Magneten und gibt HIGH-Signal an SPS
– SPS hält daraufhin Förderband an und löst Ablauf der entsprechenden Station aus

### 6.3.4 Aufbau

- Fünf Hallsensoren einzeln auf dem Rahmen des Förderbandes montiert

– Jeder Sensor dient einer Station:
* Startposition und Becherausgabe * Ausgabe Eis
* Ausgabe Zitrone
* Ausgabe Getränke

31

* Endposition

- Halterung auf Förderband über 3D-Druck realisiert und mit Nutensteinen und Schraubverbindung befestigt
- Abstand zum Schlitten kann durch Schraubverbindung im geringen Maß angepasst werden
Abbildung 33: Hallsensor | Abbildung 34: Hallsensor Halterung

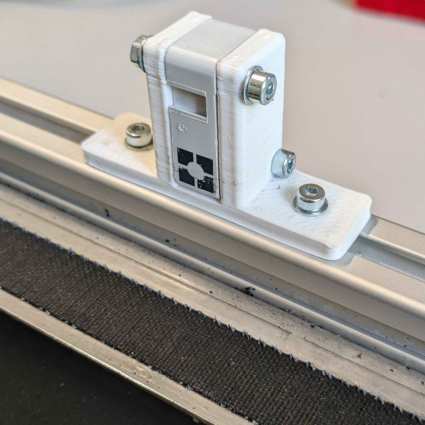
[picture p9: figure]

Abbildung 35: Hallsensor Halterung auf Förderband

### 6.3.5 Besonderheiten

Verkabelung über Förderband

- Jeder Sensor verfügt über drei Anschlussleitungen (Spannung, Masse, Datenausgang)
- Sowohl Spannungsversorgung als auch Datenausgänge können über Ein- und Ausgänge des Förderbands mit SPS verbunden werden

32

– Sensoren sind über M12-Stecker an das Förderband angeschlossen
– Spannungsversorgung und Kommunikation mit SPS erfolgt über D-Sub 25-Kabel
– Geringer Verkabelungsaufwand, da D-Sub 25-Kabel ebenfalls für die Steuerung des Förderbands dient
- D-Sub 25-Kabel wird an Terminal angeschlossen

Abbildung 36: Hallsensor Datenpanel M12 Stecker

Abbildung 37: D-Sub-Terminal

33

Pinbelegung

D-Sub 25 Pin | M12 Pin | Bezeichnung / Belegung
10 | X5 1.1 / 2.2 / 3.1 / 4.2 / 5.1 / 6.2 / 7.1 / 8.2 | Spannungsversorgung 24V
13 | X5 1.3 / 2.4 / 3.3 / 4.4 / 5.3 / 6.4 / 7.3 / 8.4 | Masse 1
14 | X5 1.2 | Datenpin Hallsensor 1
15 | X5 2.3 | Datenpin Hallsensor 2
16 | X5 3.2 | Datenpin Hallsensor 3
17 | X5 4.3 | Datenpin Hallsensor 4
18 | X5 5.2 | Datenpin Hallsensor 5

Tabelle 13: Pinbelegung Hallsensoren

### 6.4 Ablaufschiene

### 6.4.1 Stückliste

Bauteil | Anzahl
Aluminiumblech 60x11cm | 1
Profilwinkel 20x20mm | 5
M5x8 Maschinenbauschraube | 5
M5 Nutenstein | 5

Tabelle 14: Stückliste Ablaufschiene

### 6.4.2 Funktion

Schutz der Bauteile vor Getränkeüberresten / umgeschütteten Flüssigkeiten.

### 6.4.3 Betrieb

- Getränkereste in Schläuchen tropfen gelegentlich von Arm auf Förderband oder dazwischen
- Blech fängt diese zu großen Teilen ab
- Kann in Sammelschale abgeführt werden

### 6.4.4 Aufbau

- Alu-Blech leicht gewölbt und Kanten nach oben geknickt
- Ohne weiteren Schutz sammelt sich viel Rost auf Blech
- Mit schwarzer Sprühfarbe eingefärbt
- Mit Papier abgedeckt und ausgeschnittenen Schriftzug weiß angesprüht

34

- Für langen Halt der Farben dreimal mit Klarlack übersprüht
- Über 20x20 mm Profile innerhalb des Förderbandes eingeklemmt
- Klemmt genau so, dass keine Förderbandrolle am Blech schleift

Abbildung 38: Ablaufschiene in Förderband

Abbildung 39: Ablaufschiene von der Seite

### 6.4.5 Besonderheiten

- Schriftzug wurde mit Lasercutter in Papier geschnitten
- Stellt „Cocktailmaschine V3“ dar, da dritte Version der Maschine

Abbildung 40: Ablaufschiene von oben

### 6.5 Ausschankarm

Der Ausschankarm dient der spritzminimierten Ausgabe der Getränke, indem er mittels Absenkens der Ausgabeöffnungen den Abstand zwischen Becherrand und Getränkeausgabeelement verringert. Zusätzlich soll er die, zwischen den Ausgaben, austretenden Flüssigkeiten zuverlässig sammeln, um eine Verschmutzung der restlichen Maschine zu verhindern.

35

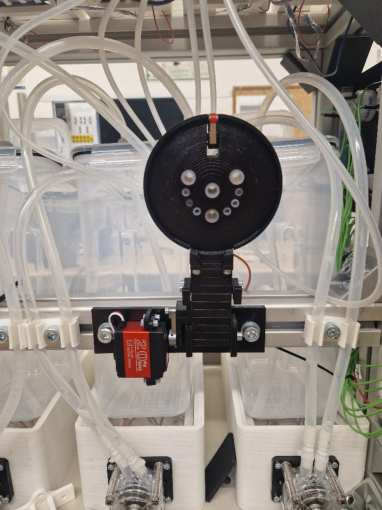
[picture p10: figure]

Abbildung 41: Ausschankarm in Wartestellung Abbildung 42: Ausschankarm in Ausgabestellung

36

### 6.5.1 Stückliste

Bauteil | Anzahl
Nutenstein P40 M8 | 2
M2,5x10 Maschinenschraube | 1
M2,5 Mutter | 1
M2,7 Unterlegscheibe | 1
M3x10 Maschinenschraube | 9
M3x16 Maschinenschraube | 2
M3,2 Unterlegscheibe | 15
M3 Federring | 1
M3x5,7 Gewindeeinsatz | 11
M4x6 Maschinenschraube | 1
M4x40 Maschinenschraube | 1
M4,3 Unterlegscheibe | 1
M4 Mutter | 1
M8x16 Maschinenschraube | 2
M8,4 Unterlegscheibe | 2
Servomotor DS3218 | 1
Micro Rollen Hebel Schalter | 1
Widerstand 11kΩ | 1
LiYv 1x0,5mm² orange (ca. 20cm) | 1
LiYv 1x0,5mm² weiß (ca. 20cm) | 1
Buchsenleiste 2,45mm (5 Buchsen) | 1
Stiftleiste 2,45mm (5 Anschlüsse) | 1
Schrumpfschlauch ca. 2cm | 7
Druckfeder aus Kuli | 1
Reinigungsschwamm | 1

Tabelle 15: Stückliste Ausschankarm

### 6.5.2 Druckanweisung

- mit Unterstützungsmaterial
- keine hohe Fülldichte
- Material: PETG

37

Abbildung 43: Gedruckte Komponenten des Ausschankarmes

### 6.5.3 Zusammenbau der einzelnen Komponenten

- Unterstützungsmaterial aus der Vertiefung am Ausschankkopf und allen Löchern entfernen
- M3x5,7 Gewindeeinsatz mit Gasbrennerflamme erwärmen und in gekennzeichnete Löcher drücken
- alle 3D gedruckten Teile nach nachfolgendem Bild verschrauben
- Leiter an Rollhebelschalterkontakte löten (wird als Schließer genutzt) und mittels Schrumpfschlauch überdecken (auch hinteren freien Kontakt mit Schrumpfschlauch versehen)
- Rollhebelschalter am Ausschankkopf so befestigen, dass dieser sich um die Verschraubung drehen kann
- Druckfeder auf das Gewinde der M4x6 Maschinenschraube aufdrehen und die Feder mittels Seidenschneider so kürzen, dass der Rollhebelschalterarm unterhalb der Unterkannte des Ausschankkopfs gedrückt wird
- Druckfeder über hinteren, mit Schrumpfschlauch abgeschirmten, Kontakt stecken
- Servomotor mit mitgelieferten Servoarm verschrauben, anschließend an Befestigungsplatte verschrauben
- Servoarm mit Arm verschrauben (Beachtung des Drehbereiches des Servomotors erforderlich!)
- Nutensteine in Aluprofil klemmen, und Befestigungsplatte anschrauben
- Verbindung zwischen Versorgung / Steuerplatine mittels Buchsenleiste und Stiftleiste herstellen

– Verdrahtung kann dem Stromlaufplan entnommen werden

- Schläuche werden zuerst durch die Zugentlastung und dann in Löcher des Ausschankarmes geschoben

38

Abbildung 44: Schaubild Verschraubung des Ausschankarms

### 6.5.4 Schnittmuster des Schwammes

Abbildung 45: Schnittmuster des Schwammes

Da die Schwammhalterungen den Schwamm auch ohne einen extra Zuschnitt fixieren können, ist dieser nicht zwingend notwendig.

### 6.5.5 Allgemeine Erläuterungen

Die Zugentlastung soll verhindern, dass durch die Auf- und Abwärtsbewegung des Ausschankarmes die Schläuche aus den Löchern im Ausschankkopf rutschen. Besonders im Moment des Tropfen-Abschüttelns ist diese zusätzliche Befestigung von großer Bedeutung.

39

### 6.6 Beleuchtung

### 6.6.1 Schaltplan Licht

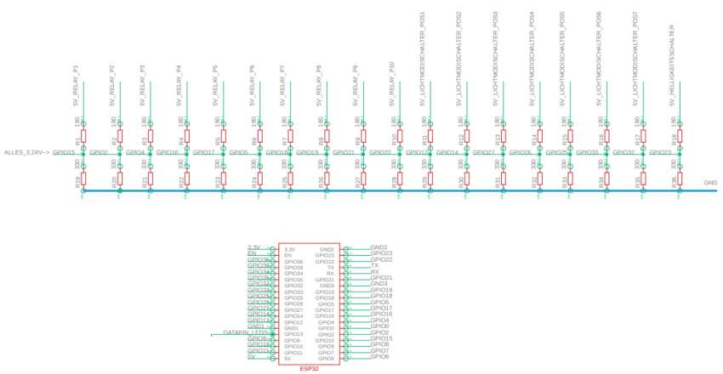
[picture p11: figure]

Abbildung 46: Schaltplan Licht

- Die Relais, welche die Pumpen steuern, schalten zusätzlich eine 5V-Leitung durch, welche an die Eingänge des ESP32s führen
– Der ESP32 erkennt dadurch, welche Pumpen aktiviert sind
- Auch vom Drehschalter auf dem Steuerpanel zum Steuern der Lichtmodi kommen 5V an die Eingänge des ESP32
- Der ESP32 benötigt nur eine Eingangsspannung von 3,3 Volt
– Es wird ein Spannungsteiler an jedem Eingang verwendet
– Widerstände: 180 Ohm : 330 Ohm, um eine Eingangsspannung von 3,24 V zu erreichen
- Zur Steuerung von 640 LEDs wird nur ein Datenpin benötigt
– GPIO13

### 6.6.2 Platine

Abbildung 47: Ansicht der Platine mit ESP

Abbildung 48: Ansicht der Platine ohne ESP, Spannungsteiler zu erkennen

40

- Kabel auf der linken Seite der Platine:

– Dateneingänge von Pumpen
– Eingang für Helligkeitstaster
- Kabel auf der rechten Seite der Platine:

– Ausgang zur Lichtsteuerung
– Eingänge für Drehschalter

### 6.6.3 Programmablauf

Um die LEDs so anzusteuern, dass die Animation in die richtige Richtung verläuft, ist es notwendig einige Umrechnungen durchzuführen. Im Normalfall werden die LEDs in der Reihenfolge 1, 2, 3, 4, 5, . . . angesteuert. In diesem Fall ist es jedoch notwendig, die LEDs in der Reihenfolge 0, 8, 16, 24, . . . anzusteuern. Diese Umrechnung passiert im Unterprogramm „Regenbogeneffekt“. Aufgrund von Begrenzungen im Netzteil kann die maximale Helligkeitseinstellung nur 100 von 255 betragen, da sonst das Netzteil nicht genug Strom bereitstellen kann.

Abbildung 49: Animationsrichtung

Grundprogramm

- Variablen werden initialisiert
- Sämtliche LEDs ausschalten, um vorherige Zustände zu löschen
- Zustand des Helligkeitstasters abfragen
- Zustand des Drehschalters abfragen

– 7 Positionen ⇒ 7 Modi

41

Abbildung 50: Grundprogramm Beleuchtung

Unterprogramm Helligkeit

- 10 Helligkeitsstufen

– Pro Knopfdruck wird die Variable counterHelligkeit um 1 erhöht, solange counterHelligkeit ≤ 10 ist

– Wenn counterHelligkeit > 10, wird counterHelligkeit = 0 gesetzt

- Pro Helligkeitsstufe wird ein LED-Panel zur Visualisierung angeschaltet

Regenbogeneffekt

- Drei Farben zur Auswahl

– Die Farbe wird abhängig vom Wert der Variablen colour gewählt

- Drei ineinander verkoppelte for-Schleifen:

– c füllt eine Spalte an LEDs
– x springt in die nächste Spalte
– i springt auf das nächste LED-Panel
– Formel: angesteuerte LED = i + 8c erlaubt es, eine Spalte der LED-Matrix nach der anderen anzuschalten
- Wenn alle LEDs mit einer Farbe gefüllt wurden, springt das Programm auf den Anfang zurück und erhöht die Variable colour, wodurch die nächste Farbe abgespielt wird

42

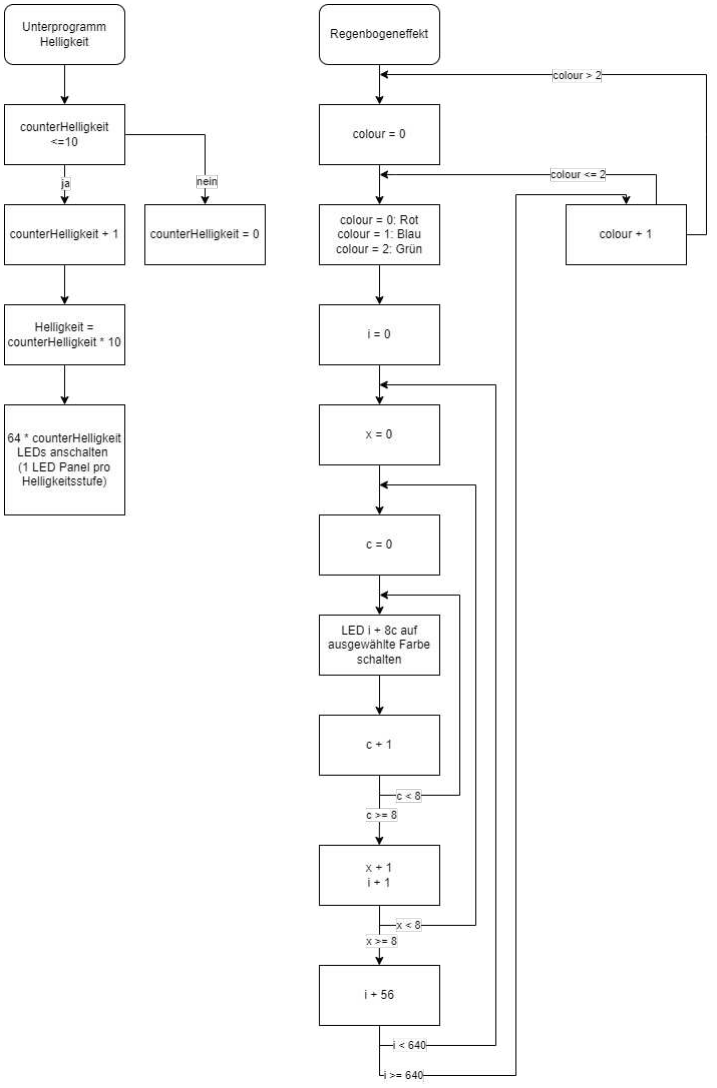
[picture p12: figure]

Abbildung 51: Unterprogramm Helligkeit und Regenbogeneffekte

43

Pumpenlicht

- Alle LEDs ausschalten, um den vorherigen Zustand zu löschen
- Wenn eine Pumpe angeht, wird ein Multiplikator m entsprechend der Pumpe aus einer Tabelle ausgewählt
- LEDs in einem Bereich von 64 × m ≤ i < 64 × (m + 1) werden angeschaltet

– Diese Formel schaltet das zu der angeschalteten Pumpe dazugehörende LED-Panel an

Zufallsmodus

- Zufallszahl Z im Bereich von 1 bis 10 mithilfe der C++ <random> Bibliothek generieren
- Eine Farbe entspricht einer Zahl
- Angeschaltetes LED-Panel entspricht der Zufallszahl Z

– Formel: 64 × (Z − 1) ≤ i < 64 × Z

- Der Delay wird mit der Formel (10 ms) × Z berechnet

– Pause bis zur nächsten Farbänderung kann zwischen 10 ms und 100 ms betragen

44

Abbildung 52: Unterprogramm Pumpenlicht und Zufallsmodus

45

Polizeifarben

- Spalten leuchten abwechselnd Blau und Rot (Spalte 1 Blau, Spalte 2 Rot, Spalte 3 Blau, . . . ).

Warmweiß pulsierend

- Warmweiße Beleuchtung mit pulsierendem Effekt:

– Die Helligkeit erhöht sich dauerhaft und wird anschließend wieder dunkler

- for-Schleife von i = 20 bis i = 100:

– Helligkeit wird auf i gestellt

- Wenn die erste for-Schleife bei 100 angekommen ist, zählt die zweite for-Schleife von 100 zurück auf 20:

– Helligkeit wird erneut auf i gestellt

Licht Blau/Grün

- for-Schleifen, die von i = 0 bis i = 639 laufen:

– Jede LED(i) wird auf Grün oder Blau gestellt

46

Abbildung 53: Unterprogramm Polizeifarben, Warmeiß Pulsierend, Grün, Blau

### 6.7 Endlagenschalter

Zum Registrieren des vom Becherspender ausgegebenen Bechers, sowie die Entnahme des fertig gemischten Cocktails an der Ausgabe, benötigt die Cocktailmixmaschine Sensoren. Diese Sensoren sollten möglichst robust gegen mechanische Einwirkung (fallende Becher) und Wasserresistent (verschüttete Getränke) sein.

47

### 6.7.1 Stückliste

Bauteil | Anzahl
Rollhebelschalter | 2
Nutenstein M8 | 1
Nutenstein M6 | 2
M2,5x16 Maschinenschraube | 2
M2,5x20 Maschinenschraube | 1
M2,7 Unterlegscheibe | 4
M2,5 Federring | 1
M2,5 Mutter | 3
M3x10 Maschinenschraube | 2
M3x20 Maschinenschraube | 2
M3,2 Unterlegscheibe | 4
M3 Mutter | 4
M3 Federring | 1
M4x10 Maschinenschraube | 1
M4,3 Unterlegscheibe | 1
M4 Mutter | 1
M6x10 Maschinenschraube | 2
M6,4 Unterlegscheibe | 2
M8x10 | 1
M8,4 Unterlegscheibe | 1
LiYv 1x0,5mm² orange (ca. 20cm) | 1
LiYv 1x0,5mm² blau (ca. 20cm) | 1
Widerstand 10kΩ | 2
Schrumpfschlauch ca.2cm | 8
Druckfeder | 1

Tabelle 16: Stückliste Endlagenschalter

### 6.7.2 Druckanweisung

- mit Unterstützungsmaterial
- keine hohe Fülldichte nötig
- Material: PLA

48

Abbildung 54: 3D-gedruckte Komponenten des Becherspendersensor

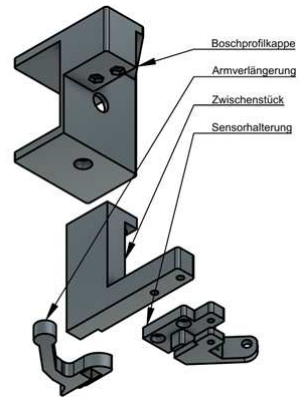
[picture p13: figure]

Abbildung 55: 3D-gedruckte Komponenten des Entnahmestationssensor

### 6.7.3 Zusammenbau der einzelnen Komponenten

- Leiter an Rollhebelschalterkontakte löten (wird als Schließer genutzt) und mittels Schrumpfschlauch überdecken (auch hinteren freien Kontakt mit Schrumpfschlauch versehen)
- 10kΩ Widerstände so verlöten, dass diese als Pulldown-Widerstände fungieren
→ Weitere Informationen dem Stromlaufplan entnehmen

Sensorik am Becherspender

- zwei M2,5 Muttern in vorgesehene Vertiefung pressen und den Rollhebelschalter von der anderen Seite mit M2,5x16 Maschinenschrauben und Unterlegscheiben verschrauben
- Armverlängerung seitlich über den Rollhebel schieben und mit Sekundenkleber fixieren
- M8 Nutenstein in Unterseite des Aluprofils einschieben und Befestigungsplatte mit einer M8x16 Maschinenschraube und Unterlegscheibe befestigen

Hinweis:
Der Sensorarm muss so ausgerichtet werden, dass er in den Fallbereich des Bechers gelangt, ohne dabei sich mit dem bewegenden Becherhalter zu verklemmen.

49

Abbildung 56: Sensor für die Becherregistrierung aus dem Becherspender

Sensorik an der Entnahme

- 3D gedruckte Teile von Unterstützungsmaterial befreien
- Rollhebelschalter mittels einer M2,5x20 Maschinenschraube, zwei Unterlegscheiben und einer M2,5 Mutter drehbar an der Sensorhalterung befestigen
- M4x10 Maschinenschraube mit Unterlegscheibe und M4 Mutter nutzen, um Druckfeder an Sensorhalterung zu befestigen (Druckfeder anschließend auf geeignete Länge mit Seidenschneider kürzen und am hinteren isolierten Rollhebelschalterkontakt verklemmen)
- Armverlängerung über den Rollhebel schieben und mit Sekundenkleber fixieren
- Sensorhalterung mit M3x20 Maschinenschrauben, Unterlegscheiben, Federringe und Muttern mit Zwischenstück verschrauben
- M3 Muttern in Vertiefung der Aluprofilkappe pressen
- Zwischenstück mit M3x10 Maschinenschrauben an Aluprofilkappe schrauben
- M6 Nutensteine auf Ober- und Unterseite des Aluprofils einschieben und Aluprofilkappe verschrauben

50

Abbildung 57: Sensor für die Registrierung der Becherentnahme

### 6.7.4 Allgemeine Erläuterungen

Um den Rollhebelschalter an der Entnahmestation mittig über dem Förderband zu platzieren, kommt ein 7cm langes Aluprofilstück zum Einsatz.

### 6.8 Schaltpanel

### 6.8.1 Stückliste

Bauteil | Anzahl
Aluminiumplatte 29x11,5 cm | 1
Profilwinkelabdeckung 80x80mm | 2
M5x10 Maschinenbauschraube | 6
M5 Federring | 6
M5 Unterlegscheibe | 6
22 FS+ Not-Knopf | 1
Knebelknopf bzw. Stufendrehschalter | 1
Mini PBS-110 Taster | 1
ZB5AA3 | 2
Miniatur Kippschalter | 5

Tabelle 17: Stückliste Schaltpanel

51

### 6.8.2 Funktion

Schnelles Stoppen der Maschine und Möglichkeit manueller Eingaben (insbesondere bei Fehlfunktionen).

### 6.8.3 Betrieb

- Notausschalter:

– „Notstop“ betitelt
– Betätigen lässt Schalter in gedrückter Position
– SPS erhält übergestelltes HIGH-Signal
– Jeglicher von SPS gesteuerter Prozess (Pumpen, Förderband) wird sofort angehalten – Durch Drehen des Schalters geht dieser zurück in die Ausgangslage
– Programm läuft an dem Punkt weiter, an dem es angehalten wurde
- Lichtschalter:

– „Licht EIN/AUS“ betitelt
– Schalter ist direkt mit der Spannungsversorgung des ESP32 (P3) und der LED-Matrizen verbunden
– Bei Betätigung werden Prozessor und LED-Matrizen vom Strom genommen
– Entsprechend ist das Licht bei Betätigung deaktiviert
– Häufige und schnelle Betätigung sollte unterlassen werden, da mögliche Schäden bei ESP32 (P3) auftreten könnten
- Stufenschalter:

– „Modi“ betitelt
– Verfügt über acht Ausgänge, unser Modell kann jedoch nur zwischen sieben Positionen wechseln (stammt aus alter Apparatur)
– Jede Position ist mit einem einzelnen Pin des ESP32 (P3) verbunden
– Ausgewählte Position gibt entsprechendes HIGH-Signal an ESP32 (P3)
– Je nach Programmierung führt jede Schalterstellung zu anderen Lichteffekten
- Taster für Helligkeit:

– „Helligkeit“ betitelt
– Bei Betätigung erhält ESP32 (P3) HIGH-Signal
– Helligkeit wird pro Signal um 10% heller gestellt
– Minimale Stufe startet bereits bei 10%
– Nach Erreichen des Maximums (100%) wird zurück auf Minimum gesprungen
- Becherspender öffnen:

– „Becherspender öffnen“ betitelt
– Bei Betätigung erhält Arduino Nano (P1) HIGH-Signal
– Beide Greifarme des Becherspenders fahren in äußerste Position – Becherspender ist entsprechend geöffnet
- Eisausgabe:

– „Eisausgabe 1x drücken“ betitelt
– Bei Betätigung erhält Arduino Nano (P1) HIGH-Signal

52

– Ablauf für Eisausgabe wird manuell gestartet

- Zitronenspender:

– „Zitronenspender EIN/AUS“ betitelt
– Bei Betätigung erhält Arduino Nano (P2) HIGH-Signal
– Stepper-Motor führt fortlaufend Vor- und Rückwärtsbewegung aus, bis Schalter in Ausgangsposition gesetzt wird
- Ausschankarm:

– „Ausschankarm hoch/runter“ betitelt
– Bei Betätigung erhält Arduino Nano (P2) HIGH-Signal – Servo-Motor am Ausschankarm fährt diesen nach unten – Bei Ausgangsposition fährt der Arm wieder nach oben
- Shotspender:

– „Shotspender Stromversorgung“ betitelt
– Direkt mit Spannungsversorgung verbunden
– Bei Betätigung wird die Platine des Shotspenders (P4) vom Strom genommen bzw. mit Strom versorgt

### 6.8.4 Aufbau

- Aluminiumplatte mit sechs integrierten M5 Muttern vorhanden gewesen
- Auf Größe von 29x11,5 cm gebracht
- Größe und Anordnung passend zu 80x80 mm Profilwinkeln an Hinterseite der Eismaschine
- Mithilfe von Profilwinkelabdeckkappen an Winkeln befestigt
- Bohrungen für Schalter und Taster angefertigt
- Schalter eingesetzt, verschraubt und mit Heißkleber verstärkt
- Jedes Schaltelement mit Etikettenband beschriftet
Abbildung 58: Schaltpanel vorne | Abbildung 59: Schaltpanel hinten

53

### 6.9 Becherspender

### 6.9.1 Stückliste

Bauteil | Anzahl
Greifarm (linker und rechter Teil, befindet sich in einer Datei) | 2
Verbindugsstück | 2
Servohalterung | 2
Endkappe oben | 1
Endkappe unten | 1
Manschette Rohr Dichtung (zwei Teile, in einer Datei) | 1
Manschette Rohr | 1
696Z Kugellager | 8
20kg Servomotor | 2
M6 Gewindestangen, ca. 200mm | 2
M6 Mutter | 28
M6 Unterlegscheibe | 20
M6 Federring | 6
M3 Gewindeeinsätze, 5,7 mm lang | 8
M6 x 25 mm Maschinenbauschraube | 2
M6 x 16 mm Maschinenbauschraube | 2
M6 Nutensteine | 4

Tabelle 18: Stückliste Becherspender

### 6.9.2 Aufbau

Der Becherspender besteht aus zwei übereinander montierten Greifarmen. Diese Greifarme werden je über einen 20kg Servomotor gesteuert, welcher über ein Verbindungsstück mit einer Seite des Greifarms verbunden ist. Durch Zahnkränze am Ende des Greifarms sind beide Arme miteinander verbunden und bewegen sich dadurch gespiegelt. Die zwei Greifarme werden mithilfe zweier M6 Gewindestangen übereinander montiert.

Druckanweisung

- kein Unterstützungsmaterial notwendig
- Fülldichte = 100%
- starkes Material wie ABS+ oder PLA+

54

### 6.9.3 Vorstellung einzelner Bauteile

Greifarm

Der Greifarm besteht aus zwei Armen, deren Bewegung durch Zahnkränze gespiegelt zusammenhängen. Dadurch ist es nur nötig, einen der beiden Arme zu bewegen, um den gesamten Greifarm zu schließen oder zu öffnen.

Benötigte Arbeitsschritte nach dem 3D-Druck:

- an vorgesehenen Stellen Kugellager mithilfe von Schraubstock einpressen

– Kugellager: 696Z (6x15x5 mm)
– kein Klebstoff verwenden
- in Vertiefungen an Oberseite nahe Kugellager M3 Gewindeeinsatz einschmelzen
- in rechteckige Vertiefungen in Innenseite des Armes eine 3D-gedruckte TPU-Dichtung einkleben

Verbindungsstück

Das Verbindungsstück stellt die Verbindung zwischen dem Servo und dem Greifarm her.

Benötigte Arbeitsschritte nach dem 3D-Druck:

- Gewindeeinsätze mit M3-Bohrer aufbohren, um Gewinde zu entfernen

– Gewindeeinsätze müssen 5,7 mm lang sein
– schützen Löcher in Verbindungsstück vor Abrieb
– beim Aufbohren der Gewindeeinsätze mit Zange die Gewindeeinsätze nicht zu stark zudrücken, verformen sich sonst

Servohalterung

- Servohalterung verbindet Servo mit Gewindestangen
- Montage nach Bild unten

Endkappen oben und unten

- Verbinden Gewindestangen mit Aluprofil und somit Maschine
- Gewindestangen mit M6 Muttern am Ende in Endkappen einpressen

Manschette Rohr und Manschette Rohr Dichtung

- erlaubt Montage von Acrylglas Rohr an Alurahmen

– Dimensionen Rohr: Außendurchmesser 90 mm, Innendurchmesser 84 mm, Länge 500 mm

- TPU-Dichtung verhindert Zerkratzen des Rohres, erhöht Stabilität
- Spannschraube nicht zu stark anziehen um Materialbruch zu verhindern

55

### 6.9.4 Montage

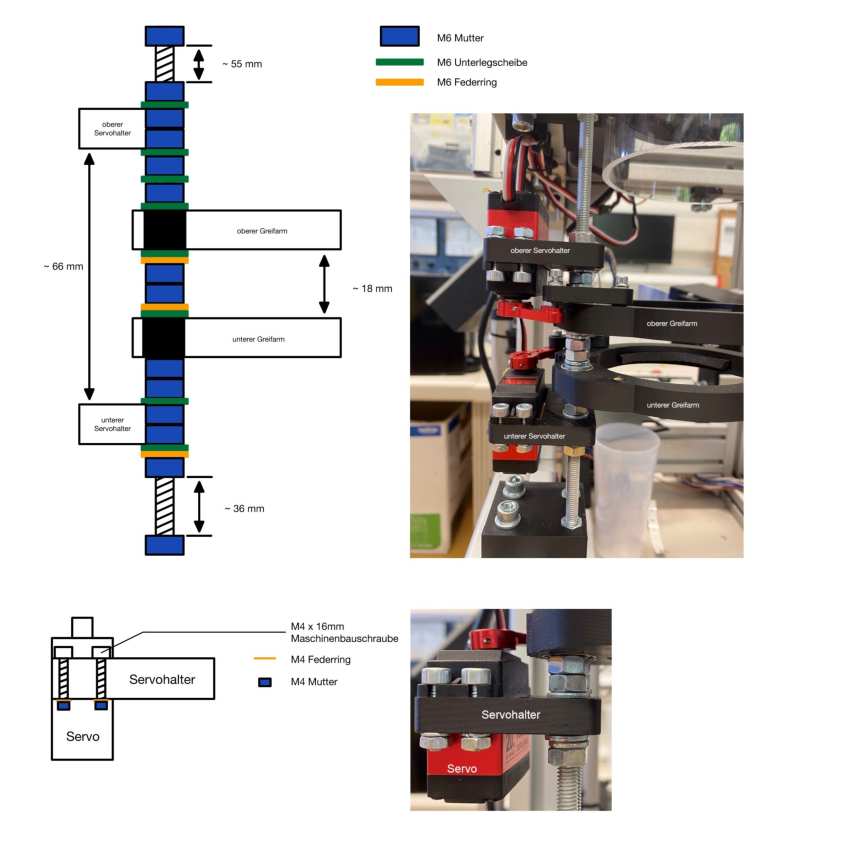
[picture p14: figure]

Abbildung 60: Becherspender

56

### 6.9.5 Platine

Abbildung 61: verkabelte Platine | Abbildung 62: Rückseite Platine

Abbildung 63: Hilfsplatine Relais

Eingänge

- Digitale Eingänge benötigten einen Pull-Down Widerstand von 220 Ohm, um Strom auf ca. 20mA zu begrenzen
- Analoger Eingang benötigt 1,2k Ohm Pull-Down-Widerstand

Hilfsplatine

- Ausgangsspannung des Arduino-Pins zur Steuerung des Relais war nicht groß genug, um dieses zu aktivieren

– Transistorverstärker mittels eines Transistors der Bauart BC548

- Arduino schaltet hiermit 24V Signal zur SPS, wenn Eis fertig ausgegeben wurde

57

Schaltplan

Abbildung 64: Schaltplan Becher-/Eisspender

### 6.9.6 Programmablauf Becher- und Eisspender

Grundprogramm

- Variablen initialisieren
- Greifarme in Ausgangsposition fahren
- auf Inputs warten wie:

– Becheranfrage von SPS
– Eisanfrage von SPS
– Schalter „Becherspender öffnen“ wird umgelegt – Knopf „Eisausgabe“ wird gedrückt
– Knopf „1x Becher“ wird gedrückt“

Becherspender öffnen

- beide Greifarme öffnen

58

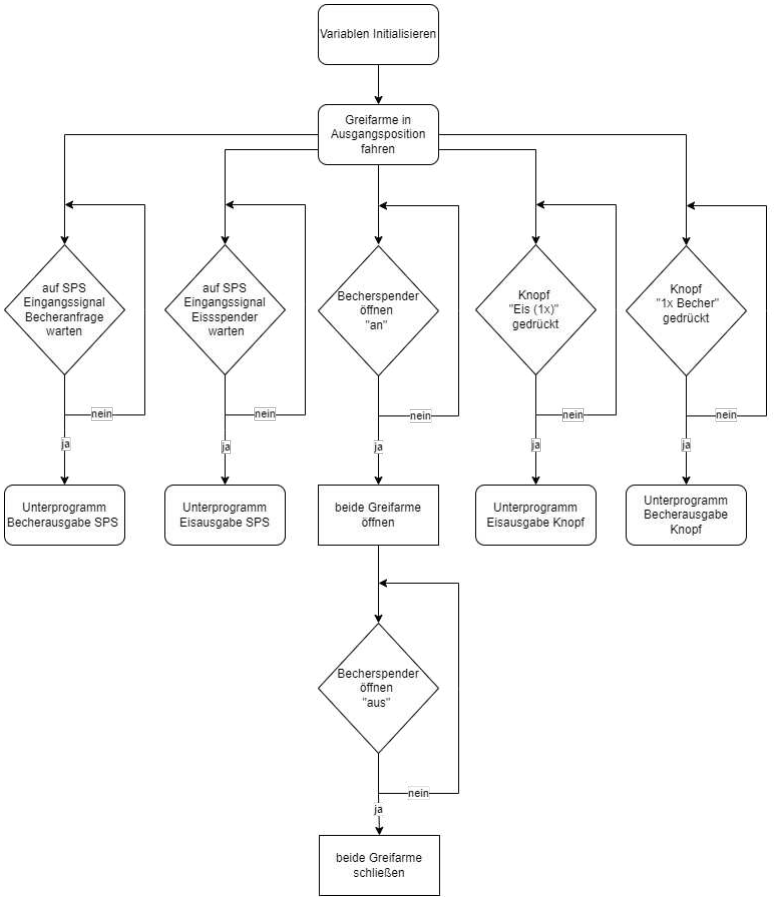
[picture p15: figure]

Abbildung 65: Grundprogramm Becher-/Eisspender

Unterprogramm Becherausgabe SPS

- Oberer Greifarm schließt sich ein wenig, um Becherstapel stabiler zu halten
- Unterer Greifarm öffnet sich, lässt einen Becher in den Becherhalter fallen
- Unterer Greifarm schließt sich wieder
- Becher rutschen erst in den unteren Greifarm nach, wenn das Eisprogramm aktiviert wurde

– Andernfalls ist der Arduino mit dem Nachladen der Becher beschäftigt, während er die Eisausgabe aktivieren sollte

59

Unterprogramm Eisausgabe SPS

- Lichtschranke aktivieren, um Eiswürfel zu erkennen
- Servomotor auf Eisausgabeknopf drücken lassen
- Helligkeitssensor der Lichtschranke abfragen, um zu erkennen, ob ein Eiswürfel durchgerutscht ist

– Kein Eiswürfel: Eisausgabe laufen lassen
– Eiswürfel erkannt: Servomotor erneut auf Eisausgabeknopf drücken lassen, um Eisausgabe zu stoppen
- Lichtschranke ausschalten
- 2 Sekunden Pause, um Eiswürfel von der Ausgaberutsche in den Becher rutschen zu lassen
- Relais für eine Sekunde aktivieren, um ein Signal an die SPS zu geben, dass die Eisausgabe beendet ist und der Becherschlitten weiterfahren kann
- Becher in den Becherspender vom oberen Greifarm in den unteren Greifarm rutschen lassen (Nachladen)

– Unteren Greifarm etwas schließen, damit der Becherstapel nicht durchrutschen kann
– Oberen Greifarm öffnen, damit der Becherstapel in den unteren Greifarm rutscht
– Unteren Greifarm etwas öffnen, um den Becherstapel in die Endposition rutschen zu lassen – Beide Greifarme in die Ausgangsposition fahren lassen

60

Abbildung 66: Unterprogramm Becherausgabe und Eisspender SPS

61

Unterprogramm Becherausgabe Knopf

- gleiche Abfolge wie bei Becherausgabe SPS
- Nachladen passiert diesmal direkt im Anschluss und nicht erst nach Eisausgabe

Unterprogramm Eisausgabe Knopf

- gleiche Abfolge wie bei Eisausgabe SPS
- kein Bechernachladen für Becherspender

Abbildung 67: Unterprogramm Eisausgabe Becherausgabe Knopf

62

### 6.9.7 Becherspender Deckel

Stückliste

Bauteil | Anzahl
Time-Of-Flight (ToF) Laser-Abstandssensor | 1
RGB-LED-Ring | 2
Arduino Nano ATmega328 | 1
Lochrasterplatine doppelseitig 70x50mm | 1
Kurzhubtaster 6x7mm | 2
Wippschalter | 1
9V Blockbatterie | 1
9V Batterieclip | 1
10 kΩ Widerstand | 2
M2x5 Maschinenbauschraube | 2
M2x35 Maschinenbauschraube | 4
M2 Mutter | 14
M3x6 Maschinenbauschraube | 9
M3x10 Maschinenbauschraube | 2
M3 Mutter | 8
M3x5,7 Gewindeeinsatz | 5
M8x40 Maschinenbauschraube | 1
M8 Unterlegscheibe | 3
M8 Mutter | 1
Kupferklebeband | 12 Streifen

Tabelle 19: Stückliste Becherspender Deckel

Funktion

Beleuchtung der Becher und Alarmierung bei unzureichendem Bechervorrat.

Betrieb

- Beleuchtung auf Unterseite strahlt Becher in Plexiglasröhre an
- Im maximalen Betrieb benötigen die Bauteile 5V / 0,3A
- Der ToF-Sensor misst durchgehend den Abstand zum höchsten Becher in der Röhre
- Wenn der Abstand einen gewissen Grenzwert erreicht:

– Licht auf Unterseite wird ausgeschaltet
– LED-Ring auf Oberseite wird aktiviert und spielt fortlaufende Animation ab

63

- Der Grenzwert beträgt aktuell 55cm (entspricht ca. 8 Bechern)

– Der Grenzwert kann einfach im Code angepasst werden

- Über die Betätigung von Taster 1 wird die Helligkeit geregelt
- Über die Betätigung von Taster 2 können verschiedene Farben auf der Unterseite ausgegeben werden

Aufbau

- Beidseitige Nutzung der Lochrasterplatine

– Hauptkomponenten (Arduino, Batterie, usw.) sowie Verkabelung auf Oberseite
– Nur notwendige Komponenten auf Unterseite (LED-Ring, ToF-Sensor)
- Für die Fixierung der LED-Ringe und des ToF-Sensors werden dünne PLA-Plättchen verwendet
- Der innere „Schaltkorpus“ wird anschließend in ein rundes Gehäuse eingesetzt
- Das Gehäuse ist auf die Plexiglasröhre angepasst und mit einem Scharnier ausgestattet
- Möglichkeit des Öffnens, um Becher nachzufüllen
- Ausschalter und Taster sind an der Scharnierhalterung montiert

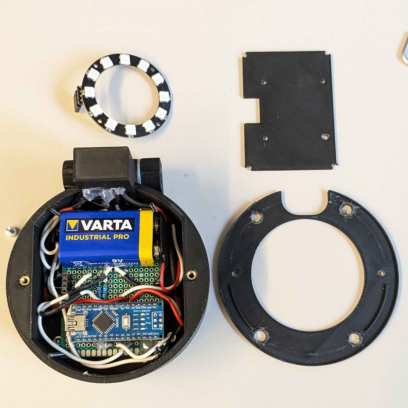
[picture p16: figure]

Abbildung 68: Becherspender Deckel innerer

Aufbau | Abbildung 69: Becherspender Deckel Außen

64

Abbildung 70: Becherspender Deckel Taster

Besonderheiten

Umsetzung Alarmbeleuchtung

- Wechsel zwischen roten und blauen Lichtern, die sich im Kreis drehen
- LEDs zeigen auf die Unterseite des Deckels
- Für bessere Sichtbarkeit der Lichter wurden drei Anpassungen vorgenommen:

– Durchsichtiges PETG als Lichtdiffusor
– Angewinkelte Deckelinnenseite
– Kupferklebeband für bessere Reflexion

65

Abbildung 71: Becherspender Deckel offener Deckel

Abbildung 72: Becherspender Deckel Alarmleuchte

Inselbetrieb

- Schaltkreis läuft als autarkes und alleinstehendes System
- Dient vor allem der Ästhetik
- Betrieb über 9V Blockbatterie
- Kapazität von 0,6 Ah
- Verbrauch bei maximaler Helligkeit 0,3 A
- Volle Batterie hält bei maximaler Helligkeit für etwa zwei Stunden

– Austausch mit Akku in Planung

66

Abbildung 73: Becherspender Deckel auf Röhre

### 6.9.8 Beleuchtung

Grundprogramm

- Variablen initialisieren
- Time of Flight Sensor initialisieren
- Alle LEDs ausschalten, um den vorherigen Zustand zu löschen
- Auf Inputs warten:

– Knopf „Helligkeit“
– Knopf „Modus“
- Abstandsmessung durchführen

Abstandsmessung

- Wenn der Abstand kleiner als 55 cm ist:

– Variable Modus wird abgefragt, je nach Modus werden verschiedene Animationen oder Farben auf dem unteren LED-Ring abgespielt
– Modus 0: LEDs leuchten weiß
– Modus 1: LEDs leuchten blau
– Modus 2: LEDs leuchten rot
– Modus 3: LEDs leuchten grün
– Modus 4: Unterprogramm RGB-Modus wird ausgeführt
- Wenn der Abstand größer als 55 cm ist:

– Oberer LED-Ring leuchtet Blau-Rot zur Warnung, dass die Becher fast leer sind – Rundumleuchte funktioniert ähnlich wie der RGB-Modus

67

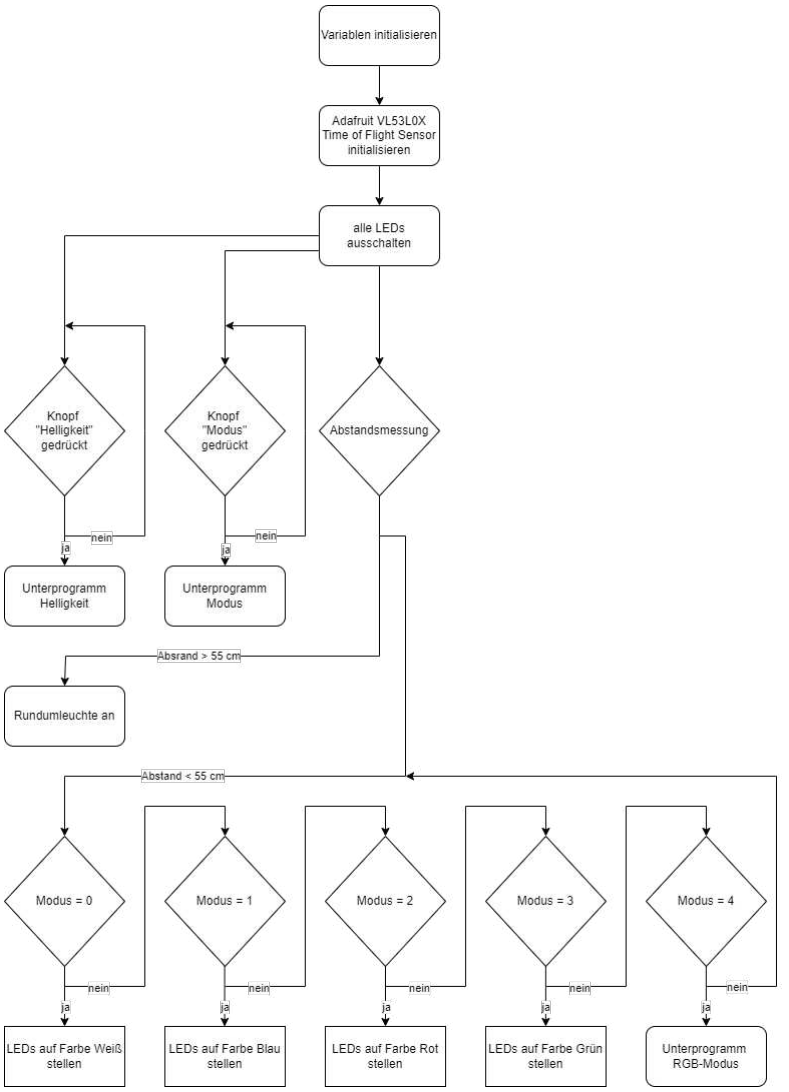
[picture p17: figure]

Abbildung 74: Grundprogramm Beleuchtung Becherspender

Unterprogramm Helligkeit

- Variable count zählt die Anzahl der Tastendrücke
- 6 Helligkeitsstufen:

68

– Helligkeit wird berechnet mit der Formel: Helligkeit = 255 / 6 * count

- LED-Ring füllt sich mit zunehmender Helligkeit:

– Berechnet mit der Formel: LEDs an = 2 * count

Unterprogramm Modus

- Variable Modus um 1 hochzählen
- Wenn Modus > 4, dann Modus = 0

Unterprogramm RGB-Modus

- Drei nacheinander ablaufende for-Schleifen:

– Schalten den LED-Ring Stück für Stück an – 1. Schleife: LEDs werden rot
– 2. Schleife: LEDs werden grün
– 3. Schleife: LEDs werden blau
- Der LED-Ring füllt sich nacheinander mit verschiedenen Farben

69

Abbildung 75: Unterprogramm Helligkeit und Modus

70

### 6.10 Eisspender

Der Eisspender setzt sich aus der Eiswürfelmaschine EM12E, einem Auslösemechanismus, einer Eiswürfelrutsche und einer Lichtschranke zusammen.

### 6.10.1 Stückliste

Bauteil | Anzahl
M8 Nutenstein | 2
M5 Nutenstein | 1
50x50x500mm U-Profil aus Aluminium | 1
M8x16 Flachschraube mit Innensechskant | 4
M8x16 Maschinenschraube | 3
M8,4 Unterlegscheibe | 4
M8 Mutter | 5
M5x16 Maschinenschraube | 5
M5,3 Unterlegscheibe | 9
M5 Mutter | 5
M4x16 Maschinenschrauben | 11
M4,3 Unterlegscheibe | 22
M4 Federring | 11
M3x16 Maschinenschraube | 4
M3,2 Unterlegscheibe | 5
M3 Mutter | 1
M2x10 Maschinenschrauben | 2
M2,2 Unterlegscheibe | 4
M2 Mutter | 1
Fotozelle | 1
Widerstand 1kΩ | 1
Laser | 1
Servomotor DES 577 | 1
LiYv 1x0,5mm² blau (ca. 20cm) | 1
LiYv 1x0,5mm² rot (ca. 20cm) | 1
LiYv 1x0,5mm² weiß (ca. 20cm) | 1
Buchsenleiste (5 Buchsen) | 1
Stiftleiste (5 Leisten) | 1

Tabelle 20: Stückliste Eisspender

71

### 6.10.2 Eiswürfelmaschine EM12E

Abbildung 76: Eiswürfelmaschine EM12E

- 230V Versorgung
- zwei Eiswürfelgrößen S (B/H=20mm/24mm) und L (B/H=23mm/25mm)
- Zubereitungszeit 6min-13min je 9 Eiswürfel
- Erkennt, wenn der Wasserbehälter leer ist und wenn das Eisfach voll ist
- Arbeitsbereich 10°C-43°C
- Kann mit externen Eiswürfeln durch obere Klappe im Gehäuse befüllt werden
- Maße: B/T/H = 424mm x 353mm x 330mm
- Gewicht: 9,5kg

Hinweis: Beim Einsatz in der Cocktailmaschine wird die Eiswürfelgröße S genutzt, da die Produktion schneller geht und eine kleinere Verklemmungsgefahr in der Eisrutsche besteht.
Die Gummifüße der Eiswürfelmaschine werden auf vier Kabelhalterungen (in Nut verdreht) gestellt. Damit ist die richtige Positionierung in der Eismaschine gewährleistet.

### 6.10.3 Eiswürfelrutsche

Bearbeitungsschritte

- Mit Stahlmaßstab Länge abmessen, gerade Linie um das U-Profil mittels Anschlagwinkel und Bleistift zeichnen
- Bügelsäge mit Metallsägeblatt zum Durchtrennen nutzen
- Scharfe Kanten mit einer Metallpfeile entgraten
- Um Biegungen durchzuführen, das Werkstück in den Schraubstock einspannen und mit einem stumpfen Gegenstand (Holzbrett) die Schläge eines Hammers übertragen
- Angezeichnete Bohrlöcher mit Körner körnen

72

- Für die Bohrung Metallbohrer nutzen, anschließend Loch mit Rundpfeile entgraten
- Bearbeitung des Alu-Profils der folgenden Skizzen entnehmen:

Abbildung 77: Eiswürfelrutsche

Abbildung 78: Zusammenbau-Schema Eiswürfelrutsche

Hochgebogenes Endstück muss so gebogen werden, dass ein Vorbeifallen der Eiswürfel verhindert wird.

73

- Verbindungsstücke an Außenwand der Eisrutschen-Segmente positionieren und mit elf M4x16 Maschinenschrauben, Unterlegscheiben und Federringen verschrauben
- Aluprofilausleger (110mm lang) für Halterung für Eiswürfelrutsche vorbereiten: M8 Gewinde in mittleres Loch schneiden und M5 Nutenstein in obere Nut einschieben
- Halterung, welche auf dem Aluprofil liegt, mit M5 Maschinenschraube und Unterlegscheibe befestigen
- Halterung an Stirnseite des Profils mit M8x16 Maschinenschraube und Unterlegscheibe anschrauben
- Mittels M8 Flachschrauben, Unterlegscheibe und Mutter die Alurutsche am Aluprofil befestigen (an der Stirnseite kommen die schrägen Unterlegscheiben zum Einsatz, da so die Kraft der Mutter gleichmäßig auf die Halterung verteilt wird)

Halterung für die Eiswürfelrutsche

Druckanweisung:

- Kein Unterstützungsmaterial nötig
- Keine hohe Fülldichte nötig
- Material: PLA

Abbildung 79: 3D-gedruckte Befestigungsplatten

Abbildung 80: 3D-gedruckte Unterlegscheibe

### 6.10.4 Lichtschranke

Bearbeitungsschritte

- Zwei Gewindeeinsätze in vorgesehene Löcher des Laserhalters und ein Gewindeeinsatz in das obere Loch des Fotozellenhalters schmelzen
- Laser in Laserhalterung mittels Heißkleber fixieren, Anschlusskabel zum unteren Loch herausführen
- Fotozelle mit Leitern, Pulldown-Widerstand und Schrumpfschlauch versehen und in Fotozellenhalterung mittels Heißkleber fixieren
- Leiter der Fotozelle ebenfalls durch das untere Loch führen

74

Abbildung 81: Laserbefestigung in Laserhaltung

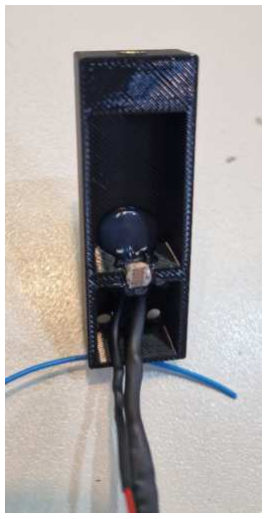
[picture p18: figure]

Abbildung 82: Fotozellenbefestigung in Fotozellenhalterung

- Lichtschranke wird oberhalb der Eiswürfelrutschen-Halterung montiert (der Laser muss durch die Löcher auf die Fotozelle scheinen)

Hinweis: Zum Schutz der Fotozelle gegen Feuchtigkeit, ist das Loch mittels Heißkleber abgedichtet. Dabei wurde in die Innenseite der Eisrutsche Malerklebeband über das Loch geklebt und von der Außenseite mit Heißkleber verfüllt.

Abbildung 83: Abgedichtetes Loch der Fotozelle

- Gegen äußere Lichteinflüsse wird über die Lichtschranke mit doppelseitigem Klebeband der Deckel geklebt
- Leiterenden an Stiftleiste löten
- Leiter der Cocktailmaschine an Buchsenleiste löten (diese Steckverbindung ist mit Isolierband umwickelt, um unbeabsichtigtes Trennen zu vermeiden).

75

Abbildung 84: Steckverbindung

3D-gedruckte Lichtschrankenkomponenten

Druckanweisung:

- Kein Unterstützungsmaterial nötig
- Keine hohe Fülldichte nötig
- Material: PLA

Abbildung 85: 3D-gedruckte Lichtschrankenkomponenten

76

### 6.10.5 Auslösemechanismus

Bearbeitungsschritte

- M8 Nutenstein in Ober- und Unterseite des Aluprofils einsetzen und Servohalterungen mittels M8x16 Maschinenschraube befestigen
- Servoarmadapter mit M2x10 Maschinenschrauben, Unterlegscheiben und Muttern am Servomotor befestigen
- Rolle mit M3x16 Maschinenschraube, Unterlegscheiben und Mutter drehbar im Servoarmadapter lagern
- Servo-Anschlusskabel mittels Stiftleiste mit Cocktailmaschine verbinden und den Servoarm so ausrichten, dass dieser den Ausgabeknopf der Eismaschine betätigt

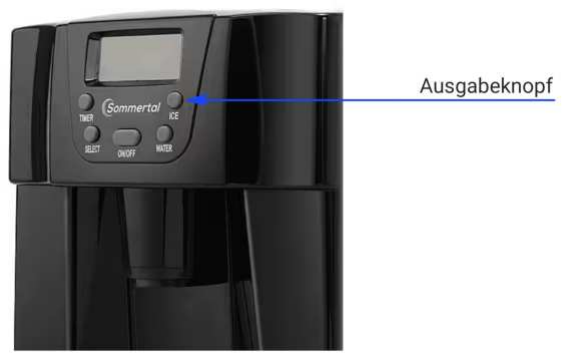
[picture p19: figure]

Abbildung 86: Ausgabeknopf

Abbildung 87: Auslösemechanismus von vorne

Abbildung 88: Auslösemechanismus von der Seite

77

3D-gedruckte Komponenten des Auslösemechanismus

Druckanweisung:

- Unterstützungsmaterial nötig
- Keine hohe Fülldichte nötig
- Material: PLA

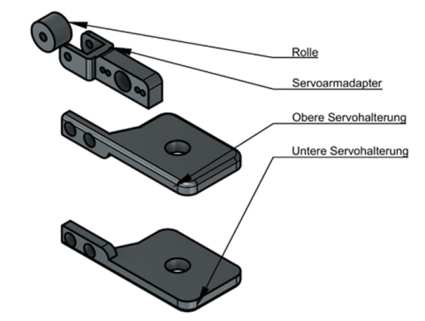
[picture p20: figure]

Abbildung 89: 3D-gedruckte Komponenten des Auslösemechanismus

78

### 6.11 Zitronenspender

### 6.11.1 Stückliste

Bauteil | Anzahl
Nema 17 Bipolar 42 Ncm(59,49 oz. In) 1,5A 42x42x38mm 4 Drähte | 1
Plexiglas 280x170mm | 1
Plexiglas 250x100mm mit Zahnrad | 1
Plexiglas 330x74mm | 1
Plexiglasrohr 80/74mm mit 330mm Länge | 1
M8 Schrauben | 11
M8 Nutenstein | 11
M6 Schraube | 1
M6 Mutter | 1
Winkel für Alu-Profil | 4
Alu-Profil 200x40x40mm | 1
Alu-Profil 232x40x40mm | 1
Alu-Profil 170x40x40mm | 1
Plexiglasrohr Halterung | 1
Plexiglas Halterung | 1
Schrittmotor Halterung | 1
Rohr Deckel | 1
Zahnrad für Stepper | 1
längliches Zahnrad (l=250mm) | 1

Tabelle 21: Stückliste Zitronenspender

Druckanweisung

- PETG eignet sich am besten für den Druck der Bauteile
- Unterstützungsmaterial bei Plexiglasrohr und Schrittmotorhalterung notwendig

### 6.11.2 Aufbau

Folgende Bauteile sind mit M8 Schrauben zu befestigen, falls nicht anders beschrieben.

- Aluprofile an die Cocktailmaschine wie im Bild mit Winkel befestigen
- Querstrebe wird im Abstand von 9cm zum Hauptrahmen an das untere Profil befestigt

79

Abbildung 90: Aufbau der Alu-Profile

- Auf die Rückseite des befestigten Aluprofils wird die Schrittmotorhalterung festgeschraubt und der Schrittmotor reingestellt

Abbildung 91: Schrittmotor von hinten

- Die vorgesehenen Kabel sind an die Buchse anzuschließen

Abbildung 92: Schrittmotorkabel

- Auf den Stepper wird das 4cm große Zahnrad gesteckt
- Darauf wird die große Plexiglas Platte mit den 2 Löchern gelegt und mit der Halterung befestigt

Abbildung 93: Ansicht mit Schrittmotor

80

- Danach wird das obere Aluprofil angebracht
- Ganz außen wird die Halterung des Plexiglasrohres befestigt

Abbildung 94: Halterung des Plexiglasrohres

- Nun wird das Plexiglasrohr in die Halterung gesteckt und mit einer M6 Schraube sowie Mutter festgeschraubt

Abbildung 95: Plexiglasrohr

– Das Plexiglasrohr sollte so weit nach unten gehen, dass 5mm Platz zwischen der Platte und dem Rohr sind

- Zuletzt wird die dünne Plexiglastrennwand in das Plexiglasrohr geschoben und der Deckel auf das Rohr gesteckt

Abbildung 96: Gesamtansicht

81

Für die Nutzung des Zitronenspenders werden 6mm bis 10mm große Zitronenscheiben benötigt

### 6.11.3 Platine des Zitronenspenders

Abbildung 97: Platine Zitronenspender und Ausschankarm

- Auf der Platine befindet sich ein Arduino Nano und ein Schrittmotortreiber A4988.

– Können bei Defekt ausgetauscht werden

- Zudem wird der Ausschankarm mit der Platine gesteuert
- Die Pinbelegung und der Anschluss der Kabel sind aus den folgenden Grafiken zu entnehmen.

Abbildung 98: Kabelanschluss

Abbildung 99: Kabelanschluss Tabelle

82

Schaltplan

Abbildung 100: Schaltplan Zitronenspender und Ausschankarm

83

### 6.11.4 Programmablauf

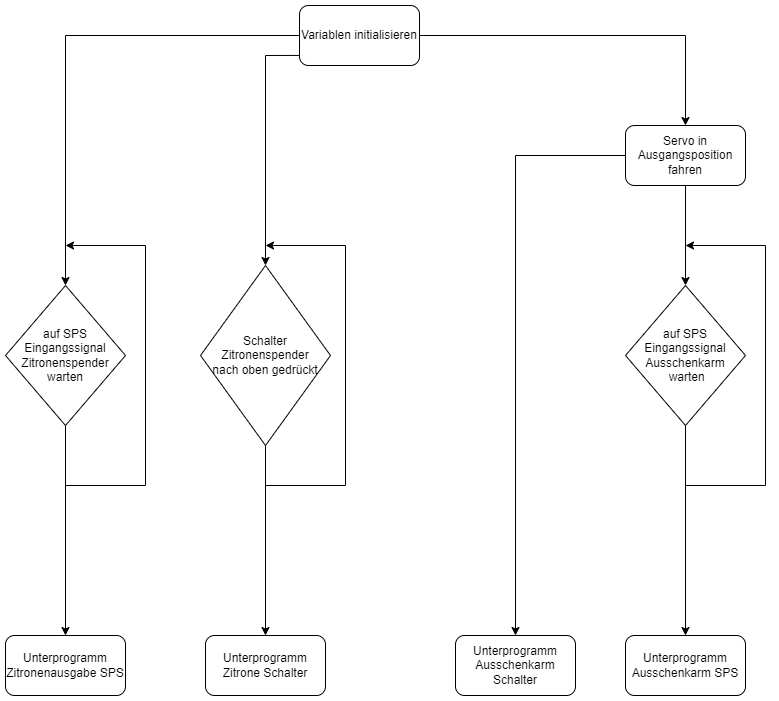
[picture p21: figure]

Abbildung 101: Gesamter Programmablaufplan

84

Abbildung 102: Unterprogramm Zitronenspender und Schalter

85

Abbildung 103: Unterprogramm Ausschankarm und Schalter

### 6.12 Shotspender

Die Cocktailmaschine wird um eine weitere Funktion ergänzt: Der Kunde / die Kundin kann zusätzlich zu einem gemischten Cocktail aus einer Auswahl von vier der sechs vorhandenen Alkoholika einen „Shot“ in ein bis sechs „Schnaps-Becher“ befüllen lassen.

### 6.12.1 Funktionsweise

Die Bestückung der Becherhalterung erfolgt manuell. Nach Auswahl der Anzahl an Bechern und des Getränkes auf dem Tastenfeld, wird zunächst durch sechs Fotowiderstände (in jeder Becherhalterung befindet sich einer) überprüft, ob sich die Anzahl an ausgewählten Bechern in den Halterungen befindet. Falls zu wenige Becher hineingestellt wurden, leuchten die noch zu besetzenden Halterungen rot. Alle bereits besetzten leuchten grün.
Wenn ausreichend Becher vorhanden sind, dreht der Servo sich auf seine Startposition (22,5°) und die Pumpe zum ausgewählten Getränk wird gestartet. Der erste Becher wird vollgefüllt und anschließend dreht die Pumpe 100 Millisekunden zurück, um nicht zu tropfen. Danach wird der Servomotor gestartet

86 um den Ausschankarm um 22,5°nach links zu drehen. Hier wird der nächste Becher befüllt. Je nach ausgewählter Becheranzahl, wird dieser Vorgang bis zu sechsmal wiederholt. Nach dem letzten Mal wird der Ausschankarm wieder zur Ausgangsposition gedreht.

Die Bedienung ist weitgehend selbsterklärend und wird Menü-geführt:

### 1. Getränk wählen

### 2. Anzahl Becher wählen

### 3. Becher reinstellen

### 4. Auswahl bestätigen

### 6.12.2 Stückliste

Bauteil | Anzahl
Anzeige- und Displayfassung | 1
Anzeige- und Displayhalterung | 1
Anzeigefassung | 1
Arduinohalterung | 1
Ausschankarm | 1
Becherhalterung | 1
Servohalterung | 1
Servofassung | 1
Pumpenhalterung | 1
Fotowiderstand | 6
L298N Motor Driver Controler Board Module | 2
4 x 4 Matrix Tastenfeld | 1
Klappträger B 47 x H 60 x T 200 mm verzinkt | 2
Mini Schlauchpumpe 12V | 4
Arduino mega-2560-R3 | 1
Servo C 5077 | 1
WS2812 ECO LEDs RGB Individuell adressierbar | 1
M8 Nutenstein | 2
M8x16 Maschinenbauschraube | 2
M6 Nutenstein | 10
M6x10 Maschinenbauschraube | 10
M4 Nutenstein | 4
M4x10 Maschinenbauschraube | 4
M2x5 Maschinenbauschraube | 8
M2 Mutter | 8

Tabelle 22: Stückliste Shotspender

87

### 6.12.3 Skizzen der Bauteile

Abbildung 104: Anzeige- und Displayfassung

Abbildung 105: Anzeige- und Displayhalterung

88

Abbildung 106: Anzeigefassung

Abbildung 107: Arduinohalterung

89

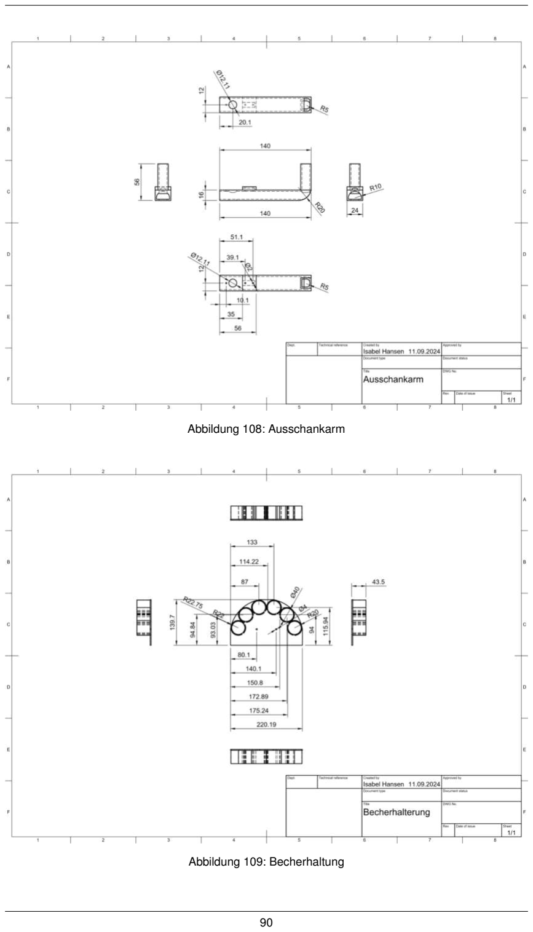
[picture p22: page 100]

Abbildung 108: Ausschankarm

Abbildung 109: Becherhaltung

90

Abbildung 110: Servohalterung

Abbildung 111: Servofassung

91

Abbildung 112: Pumpenhalterung

### 6.12.4 Aufbau

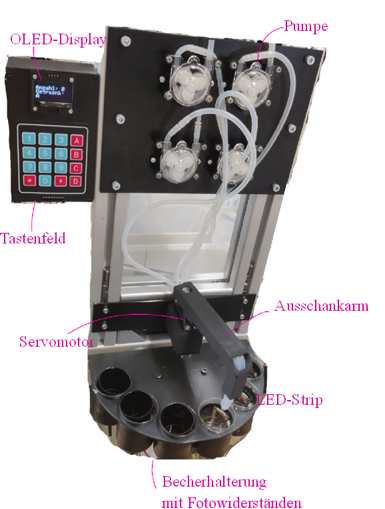
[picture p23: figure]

Abbildung 113: Aufbau des Shotspenders

- Steuerung der Cocktailmaschine über SPS.

– Funktionsanteile auf verschiedene Arduino-Mikrocontroller ausgelagert.

- Steuerung des Shotspenders über Arduino Mega 2560 R3 Board.
- Kompatibilität der Apparatur des Shotspenders mit dem Arduino erforderlich.

92

- Tastenfeld (4x4 Matrix) zur Eingabe der Becheranzahl und Getränkeauswahl sowie zur Bestätigung.

– Über acht Datenpins mit dem Arduino verbunden.

- Anzeige zur Bedienungshilfe auf SSD1306 I2C OLED Graphic Display.

– Display-Anschlüsse: SDA, SCL, VCC (5V), GND.

- Bechererkennung durch Fotowiderstände im Boden der Becherhalterung.

– Fotowiderstände ändern elektrischen Widerstand entsprechend der Lichtmenge.
– Fotowiderstände für Maximalspannung von 150 V ausgelegt.
- Kalibrierung der Grenzwerte des Lichtsensors durch separaten Taster.
- LEDs an den Becherhalterungen gehören zu „LED RGB individuell adressierbaren Lichtstreifen“.

– LED-Farben abhängig vom Becherstatus (grün/rot).

- LED-Streifen benötigt nur einen Daten-Pin, GND und 5V

– platzsparend am Arduino

- Vier Minischlauchpumpen für Flüssigkeitsbeförderung von Behältern zu den Bechern

– Pumpen werden mit 12V Gleichspannung betrieben

- Steuerung der Pumpen über zwei doppelte H-Brücken

– Pumpen drehen kurz zurück, um Tropfen zu verhindern
– Flüssigkeitsmenge auf 30 ml eingestellt
– H-Brücke besteht aus vier MOSFETs und vier Sperrdioden
– T1 und T4 offen: Strom fließt durch Motor (Pumpe) in eine Richtung
– T3 und T2 offen: Strom fließt in entgegengesetzte Richtung
– Durch Umdrehen der Stromrichtung: Rückdrehen der Pumpen nach Pumpvorgang (Flüssigkeitsreste werden zurückgepumpt)
- Servo C5077 für Drehung des Ausschankarms

– Servo hat bei 5V ein Stellmoment von ca. 50 N/cm

- Gesamter Shotspender (außer Pumpen) wird mit 5V betrieben
- Mechanische Bauteile der Shotspender-Halterung mittels 3D-Druck hergestellt

Abbildung 114: Grundaufbau Vierquadrantensteller

93

### 6.12.5 Programmierung

Programmablaufplan

Abbildung 115: Programmablauf Shotspender

94

Abbildung 116: Unterprogramm Bestellvorgang

95

Anforderungen

- Pumpenansteuerung per Arduino Mega 2560 R3 für vier Pumpen, mit zwischengeschalteten H-Brücken zur Steuerung von Drehrichtung und Geschwindigkeit.
- Einbettung und Eingabeverarbeitung eines Matrix-Eingabefeldes.
- Anzeigemöglichkeit auf OLED Display.
- Verarbeitung der angeschlossenen Lichtsensoren.

– Dadurch soll erkennbar sein, ob und wo sich Becher in der Halterung befinden.

- Einbettung eines Tasters zur Kalibrierung des Sensor-Schwellwerts.
- Einbettung und Steuerung des individuell adressierbaren LED-RGB-Lichtstreifens (vier LEDs pro Becherhalter).
- Servoansteuerung.

Durchführung

- Programmierung mithilfe der Arduino IDE
- Aktualisierung und Einbettung des OLED-Displays mithilfe der Bibliothek Adafruit_SH110X

– Ergänzt durch Adafruit_GFX zur Pixelsteuerung, um Größe, Position der Buchstaben und
Zahlen sowie die Textfarbe festzulegen
- Steuerung des LED-RGB-individuell-adressierbaren Lichtstreifens mithilfe der Bibliothek Adafruit_NeoPixel

– Farbe, Helligkeit, Leuchtzeitpunkt und -raum jeder einzelnen LED regelbar

- Für den Servomotor: Bibliothek Servo
- Kommunikation zwischen Matrix-Eingabefeld und Arduino mithilfe der Bibliothek Keypad
- Kalibrierung der Sensoren erfolgt durch Ermittlung des gleitenden Durchschnitts der letzten zwanzig Sensormessungen

– Neuer Sensorwert == Durchschnitt - 15 ⇒ Becher wurde reingestellt
– Neuer Sensorwert == Durchschnitt + 15 ⇒ Becher wurde wieder rausgenommen
- Der gesamte restliche Ablauf wird durch eine State-Machine gesteuert

Messwerte der Sensoren:

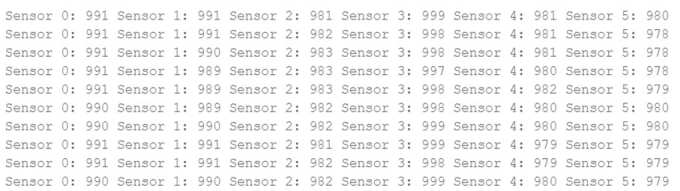
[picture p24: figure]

Abbildung 117: Messwerte der Sensoren ohne Becher

96

Abbildung 118: Messwerte der Sensoren mit Bechern

97

### 6.12.6 Platine

Abbildung 119: Shotspender-Platine

### 6.12.7 Fazit

Der Shotspender erweitert den bestehenden Cocktailspender um eine neue Funktion, die es ermöglicht, verschiedene Getränke präzise in mehrere Shot-Becher abzufüllen. Die Umsetzung erfolgte mithilfe des Arduino-Mega-2560-R3, der durch seine zahlreichen Ein- und Ausgänge den Anforderungen gerecht wird. Der Einsatz eines adressierbaren LED-Lichtstreifens verringerte die benötigte Pin-Anzahl

98 erheblich und steigerte so die Effizienz des Systems.
Anfängliche Probleme, wie die Erkennung der Becher aufgrund der Nutzung durchsichtiger Becher, konnten durch den Wechsel zu schwarzen Bechern und eine angepasste Positionierung der Sensoren behoben werden. Dies stellt sicher, dass belegte und freie Halterungen zuverlässig unterschieden werden können.

### 6.13 Bestelltafel

### 6.13.1 Stückliste

Bauteil | Anzahl
PowerPanel für SPS 7 Zoll | 1
HKC LED Monitor 18,5 Zoll | 1
Ethernetkabel | 1
Kaltgerätekabel | 1
VGA-Kabel | 1
flacher Winkel 90°, 16x16cm | 2
M6x16 Maschinenbauschraube | 12
M6 Unterlegscheibe | 12
M6 Nutenstein | 12
M8x16 Maschinenbauschraube | 4
M8x25 Maschinenbauschraube | 1
M8 Nutenstein | 4

Tabelle 23: Stückliste Bestelltafel

### 6.13.2 Funktion

Eingabe der Bestellung und Anzeige des Bestellmenüs.

### 6.13.3 Betrieb

Eingabe der Bestellung

- PowerPanel über Ethernetkabel mit SPS verbunden
- Verschiedenste Eingaben möglich
- Anzeige des aktuellen Status der Bestellung
- Im Betrieb benötigt Panel 24V / 20W

Anzeige des Bestellmenüs

- Anzeige wird über HKC LED Monitor realisiert
- Zusätzliche Anzeige zum Bestellmenü, für simultane Nutzung beider Medien

99

- Über VGA mit externen Rechner verbunden, welcher Bildschirm dupliziert
- Im Betrieb benötigt Monitor 230V / 1,1A

Abbildung 120: Menü Monitor

Abbildung 121: Rückseite Monitor

### 6.13.4 Aufbau

- Monitor über eigene Aufhängung mit Alu-Profilen verbunden
- Wird zusätzlich durch Profilendkappen in Position gehalten
- PowerPanel in 3D-gedruckter Struktur versenkt

– Ist um 45°nach oben gehoben
– Dient der leichteren Interaktion mit Panel
- Alu-Profile über zwei Flachwinkel miteinander verbunden

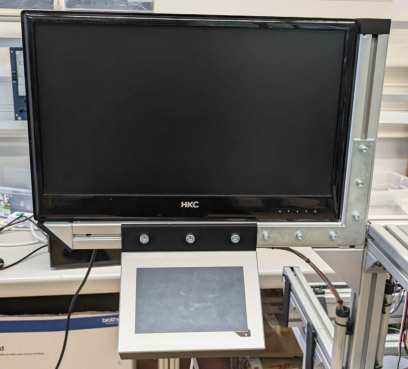
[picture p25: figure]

Abbildung 122: Aufbau vorne

Abbildung 123: Aufbau hinten

### 6.13.5 Besonderheiten

Rotierbares System

- Gesamter Aufbau der Bestelleinheit ist über eine Schraube mit einemProfilwinkel verbunden

100

- Da nur eine Schraube eingeführt wurde, ist System einklappbar
- Verringert bei Transport die Länge der Maschine
- Bei längerer Nutzung sollte Schraube jedoch angezogen werden

Zugang zu Monitoreinstellung

- Manuelle, interne Einstellungen des Monitors (Ein/Aus, Quelle, Helligkeit, usw.) unterhalb am Rahmen angebracht
- Für Interaktion sind fünf Löcher durch das Alu-Profil gebohrt
- Bisher genutze Methode: Inbusschlüssel als Tastverlängerung nutzen

Abbildung 124: Löcher im Profil

Externes Bestellmenü

- Anzeige für Monitor durch externen Laptop und Powerpoint-Präsentation realisiert
- Bei weiterführender Entwicklung ggf. durch anderes, internes Medium ersetzen und mit SPS koppeln

## 7 Programmierung der SPS

### 7.1 Technische Rahmenbedingungen

### 7.1.1 B&R Firma generell

In dem folgendem Abschnitt werden Produkte von B&R verwendet. Die B&R Industrial Automation GmbH ist ein österreichisches Technologieunternehmen der Automatisierungstechnik und Teil der ABB-Gruppe mit Hauptsitz in Eggelsberg bei Braunau in Oberösterreich und wurde 1979 gegründet. Das Unternehmen bietet Gesamtlösungen in den Bereichen Maschinen- und Fabrikautomation, Antriebs- und Steuerungstechnik, Visualisierung und integrierte Sicherheitstechnik sowie Lösungen für die Kommunikation im Industrial IoT – allen voran OPC UA, POWERLINK und der offene Standard openSAFETY an.

101

### 7.1.2 Verwendete Hardware-Komponenten

Zur Programmierung der Cocktailmaschine wurde eine B&R SPS X20CP1382 verwendet.

Weitere Komponenten:

- Zusatzmodul: X20CDO8322 (für weitere Digitale Outputs)
- Display: 6PPT30.0702-20W (zur Bedienung der Maschine)
- Hall Sensor: BALLUFF - BES 517-351-NO-C-03 (zur Erkennung der Einzelstationen)

### 7.1.3 Automation Studio

Zur Programmierung wurde das von B&R entwickelte Automation Studio verwendet. Diese Entwicklungsumgebung bietet neben der Programmierumgebung auch die Möglichkeit, eine SPS lokal zu simulieren sowie durch mehrere Diagnosewerkzeuge auf SPS-interne Informationen zuzugreifen.

Der in den folgenden Abschnitten besprochene Code kann unter https://github.com/UniversityMasarum/Cocktail-Mix-Maschine-V3 heruntergeladen werden. Dieser ist in dem Unterverzeichnis Programmierung zu
finden und kann in Automation Studio durch das Projektfile, X20CP1382.apj, geladen werden.

Zum grundlegenden Einfinden in Automation Studio sowie zum Bearbeiten des Projekts ist es zu empfehlen, sich die Bilderdokumentation unter Nextcloud anzusehen. Hier sind viele verwendeten Konzepte und deren Umsetzung in Automation Studio näher beschrieben.

Eine umfänglichere Dokumentation ist in Automation Studio intern zu finden. Diese nennt sich B&R Help Explorer – Automation Help. Diese kann über den Reiter Hilfe/Zeige Help Explorer gefunden werden.

Logical View

Die Logical View stellt die hardwareunabhängige Ansicht der Anwendung dar. Darin werden die Programme, sowie deren zugehörige Elemente wie Variablendeklarationen und Bibliotheken verwaltet.

Configuration View

Die Configuration View stellt die hardwareabhängige Sicht der Anwendung dar. Darin werden unter anderem die Hardwarekonfiguration und die Zykluszeiten der Programme verwaltet.

Physical View

In der Physical View wird die aktive Konfiguration des Hardwareaufbaus verwaltet. Darin wird unter anderem die Anordnung der Module und die Konfiguration der Inputs und Outputs festgelegt.

### 7.1.4 Strukturierter Text

Strukturierter Text ist eine textuelle Programmiersprache der Norm IEC 61131-3.
In diesem Projekt wurde ausschließlich Strukturierter Text zur Programmierung der SPS verwendet.

102

### 7.1.5 Netzwerkeinstellungen

Zum Verbinden der Cocktailmaschine müssen folgende Änderungen an den Netzwerkeinstellungen an der Ethernet Schnittstelle des Rechners durchgeführt werden:

- IP-Adresse: 192.168.10.99
- Subnetzmaske: 255.255.255.0

### 7.2 Website

### 7.2.1 B&R Website generell - MappView

Bei B&R gibt es die Möglichkeit zusätzlich zu den einzelnen generischen analogen- sowie digitalen Inputs auch Eingänge über eine, in die B&R Automatisierungsumgebung integrierte Website zu schalten. Diese Website heißt MappView.

Der Vorteil bei der Nutzung von MappView ergibt sich durch die Schnittstelle, Ethernet. Diese ermöglicht es mehrere Variablen beinahe nahtlos und parallel zu verändern.

Ein weiterer Vorteil ist, dass sich der Automatisierer voll auf seine Kernkompetenz konzentrieren kann, da die Umsetzung möglichst effizient und einfach gestaltet wird. Technisch funktioniert die Website mit HTML5, CSS3 und JavaScript. Die Seiten & Widgets werden in der gewohnten Umgebung von Automation Studio erstellt. Dort stehen integrierte Visualisierungs-Bausteine, sogenannte Widgets, zur Verfügung, die alle Funktionen einer Maschinen-Benutzeroberfläche abdecken. Die Widgets werden per Drag-and-drop auf die gewünschte Seite gezogen und dort einfach parametriert.

Hierbei ist es allerdings nicht möglich die Funktionen und das Aussehen der einzelnen Widgets & Seiten über die vorgegebenen Parameter hinaus individuell umzuschreiben. Deshalb müssen für umfangreichere Events mit mehreren Änderungen parallel Eventbindings verwendet werden.

opcUA Variablen

opcUA sind Variablen, die zur Laufzeit von der Weboberfläche verändert werden können. Dafür müssen diese Variablen aktiviert werden. Diese können in der Datei AS\Physical\Config1\X20CP1382\ Connectivity\OpcUA\OpcUaMap.uad als opcUA Variable gekennzeichnet werden.

### 7.2.2 Praktische Umsetzung der Weboberfläche

Die Hauptaufgabe der Website ist die Bestellung von alkoholischen Getränken sowie von Softdrinks. Allerdings können über die Schaltfläche zusätzlich noch allgemeine Informationen zur Cocktailmaschine über das Wiki aufgerufen werden. Des Weiteren gibt es die Möglichkeit durch die Eingabe des Passworts „student42“ in das Reinigungsprogramm zu kommen, auf welcher weitere Funktionen, Debugging und Reinigung verfügbar sind.
In den folgenden Abschnitten wird auf die einzelnen Webpages und deren Struktur im Detail eingegangen.

103

### 7.3 Hauptnavigation

Abbildung 125: Hauptnavigation

Die Hauptnavigation ist für die grundlegende Navigation der einzelnen Pages zuständig. Hierbei handelt es sich bei den vier Buttons um widgets.brease.navigationButton. Diese Buttons sind in dem B&R Werkzeugkasten für eine Navigation zwischen den Webseiten möglich. Die Hauptnavigation hat die pageID(page_0). Eine pageID ist ein eindeutiger Verweis auf eine spezifische Seite.

Hierbei verweist die Schaltfläche:
„Softdrinks“ auf pageID(page_1)
„Alkoholische Cocktails“ auf pageID(page_2)
„Reinigungsprogramm“ auf pageID(page_3)
„Informationen Wiki“ auf pageID(page_4)

Wie auf dem Bild zu sehen ist, ist das Reinigungsprogramm standardmäßig ausgeblendet. Dieses Widget kann eingeblendet werden, indem in das Passwortfeld das Passwort „student42“ eingegeben wird.

Dieses eingegebene Passwort wird in einer Variable abgespeichert, welche dauerhaft im Hauptprogramm überprüft wird. Wenn diese dem gesetzten Passwort entspricht, wird die Seite eingeblendet, da diese an den Parameter enable des NavigationButtons weitergegeben wird. Das bedeutet allerdings auch, dass bei einer erneuten Veränderung diese Schaltfläche wieder ausgeblendet wird. Im Hauptprogramm ist diese Funktion wie Folgt implementiert.

Abbildung 126: Code Passwortabfrage

Dieses Passwort verhindert, dass Unbefugte auf die interne Steuerung zugreifen können. Im nächsten Absatz gebe ich an, auf welche Funktionen ein Facharbeiter über diese Schaltfläche Zugriff hat.
Zum Anpassen des Passworts kann dieses unter variables.var, im program, durch verändern des Standardwerts angepasst werden.

104

### 7.3.1 Reinigungsprogramm

Abbildung 127: Website Reinigungsprogramm

Durch das Reinigungsprogramm können Ausgänge und Variablen zum Reinigen sowie zum Debuggen der Maschine geschaltet werden.

Für alle Funktionen auf der Seite muss der Reinigungsmodus aktiviert werden. Das soll als eine Art Zweifaktor-Überprüfung dienen. Das bedeutet, dass sich nur durch Aktivierung zweier Schalter die ausgewählte Funktion ausführen lässt.

Hierbei lassen sich die Funktionen in folgende Kategorien unterscheiden:

- Pumpensteuerung
- Laufbandsteuerung
- Reset

Im Folgenden wird die Funktion der einzelnen ToggleSwitch Widgets näher erklärt. In unserem Fall sind Widget.brease.ToggleSwitch Schalter, die Variablen verändern und gleichzeitig Feedback über die veränderte Variable an den Nutzer geben. Das heißt, über den Anschlag des einzelnen Knopfes kann der Nutzer direkt sehen, welche Eingänge geschaltet sind und welche wiederum deaktiviert sind.

Pumpensteuerung
Die Pumpensteuerungswidgets, Pumpe 1 bis 10, dienen als eine manuelle Ansteuerung der einzelnen Pumpen für die Zutatenbehälter. Das Pumpensteuerungswidget „Alle Pumpen AN/AUS“ Schaltet alle Pumpen gleichzeitig AN bzw. AUS.

Laufbandsteuerung
Die Laufbandsteuerung besteht aus drei Widgets. Zwei SwitchButtons, welche die Richtung des Laufbands bestimmt und einen ToggleButton der die SwitchButtons zurücksetzt. Eine Aktivierung eines SwitchButtons führt zum Rücksetzen des jeweils anderen SwitchButtons, sodass nie beide Laufbandrichtungen gleichzeitig auftreten können.

RESET AUF START
Wenn dieser Knopf aktiviert wird, wird die Switch Case im Hauptprogramm verändert und die in den Variablen erhaltenen Informationen auf die letzte Station gesetzt.

105

Abbildung 128: Website Auswahl für den Endnutzer

### 7.3.2 Die Auswahl für den Endnutzer

Die relevanten Seiten für den Nutzer beschränken sich auf die Seiten Softdrinks, pageID(page_1) und Alkoholische Cocktails, pageID (page_2). Hier können mithilfe der einzelnen ToggleButtons Cocktails ausgewählt werden. Wenn der gewünschte Cocktail ausgewählt wurde, wird über ein Eventbinding die Cocktailvariable umgeschaltet, d.h. der Cocktail wird gestartet und der Monitor schaltet auf den Wartebalken um.

Die auf die einzelnen ToggleButtons angewandten Eventbindings werden im Unterkapitel Eventbindings erklärt.

### 7.3.3 Der Ladebalken

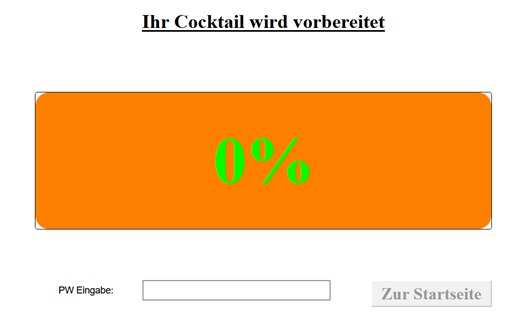
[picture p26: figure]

Abbildung 129: Website Ladebalken

Nach der Bestellung eines Getränkes, gibt es für den Kunden noch einen Ladebalken. Er dient als Feedback, dass der Bestellvorgang funktioniert hat. Dieser zeigt den Fortschritt an, bis das Getränk bereit zur Ausgabe ist. Diese Seite hat die PageID(page_5).

Falls es während des Ausgabevorganges zu einem Fehler kommt, kann über das Passwort „student42“ der navigationButton Zur Startseite aktiviert werden. Von dort kann über das Reinigungsprogramm das Programm wieder zurückgesetzt werden.

106

### 7.3.4 Eventbindings

Eventbindings sind an Ereignisse gebunden. Diese Eventbindings können damit Variablen setzen, ändern oder auch die Website umschalten, ohne in die festen Taktzeiten der SPS einzugreifen. Dadurch konnte in dem Fall der Cocktailmaschine gleichzeitig eine Variable gesetzt werden sowie auf eine andere Website gewechselt werden. Mit Eventbindings können Limitationen der MappView ausgeglichen werden. Die Eventbindings befinden sich im Projekt Explorer in der ConfigurationView unter dem Verzeichnis mappView.

Während die Widgets in MappView durch eine begrenzte Anzahl an, für den Nutzer veränderbaren Parametern umschalten können(meistens nur eine Variable anpassen oder eine Website umschalten), können mit den Eventbindings gleichzeitig mehrere Events ausgelöst werden.

Im folgenden Bild sieht man ein Eventbinding, wie es auch bei der Cocktailmaschine genutzt wird. Hierbei ist zu beachten, dass alle im Projekt verwendeten Eventbindings eine ähnliche Struktur besitzen.

Abbildung 130: Website Eventbindings

Source: B&R Help Explorer

### 7.4 Code

### 7.4.1 Unterprogramme

Der Code teilt sich in drei Unterprogramme, welche sich ausschließlich im Cyclic-Teil des Programmes
befinden. Program, Program1 und Zufall.

Program
Ist für die Funktionsweise, d.h. die Automatenlogik zuständig sowie für Funktionen, die für die Fehlerbehebung notwendig sind.

Program1
Ist für das Mischen der einzelnen Cocktails zuständig.

Zufall
Führt die zur Ausgabe des Zufallscocktails nötigen Berechnungen durch.

Zykluszeiten der Unterprograme

- Program – 100ms
- Program1 – 100ms
- Zufall – 1000ms

107

### 7.4.2 Benennung der Variablen

Die Variablen findet man unter dem Unterverzeichnis Variablen.var des jeweiligen Programms. Außerdem befinden sich in Global.var, Variablen, auf die aus jedem Programm zugegriffen werden kann.

Die Variablen und deren Funktion im Programm sind gut erkenntlich durch ihre zumeist intuitiven Namen. Darüber hinaus wurde auch jede Variable durch ihre Endung einem bestimmten Zweck zugeteilt, was in der folgenden Auflistung der einzelnen Endungen ersichtlich wird.

- _DO → Eine Variable, die einen digitalen Ausgang schaltet.
- _DI → Eine Variable, die einen digitalen Eingang schaltet.
- _var → Eine Variable, die nicht auf einen Eingang geschaltet ist.

Alle Variablen ohne spezifische Endung werden auch nicht direkt auf einen Eingang geschalten.

Darüber hinaus gibt es zu jeder Variable in der Spalte Description zusätzlich noch eine detailliertere Erklärung zur Funktion der Variable.

### 7.4.3 Program - Grundlegender Ablauf

Die Cocktailmaschine hat grundlegend 5 Stationen.

- Becherstation
- Eisstation
- Zitronenstation
- Cocktailstation
- Becherausgabe

Diese werden während der Laufzeit durch ein Laufband angefahren. Zur Detektion der einzelnen Stationen wird ein Hallsensor verwendet. Dieser Hallsensor reagiert auf einen Magneten, der an den Schlitten angebracht wird. Der gewählte Hallsensor war hierbei der BALLUFF - BES 517-351-NO-C-
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

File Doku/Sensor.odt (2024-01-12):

Braun = +

Blau = -

Schwarz = N/0

4,7 kOhm widerstand zwischen Blau und schwarz

Messung der Spannung von Schwarz auf Blau über den Widerstand

M8-Stecker 3polig war davor dran

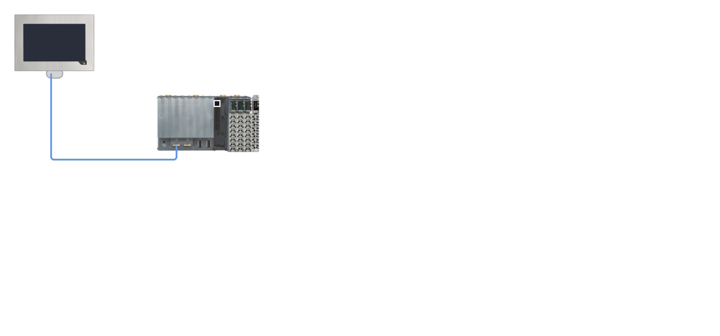
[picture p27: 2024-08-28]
Programmierung/AS/Physical/Config1/Hardware.jpg

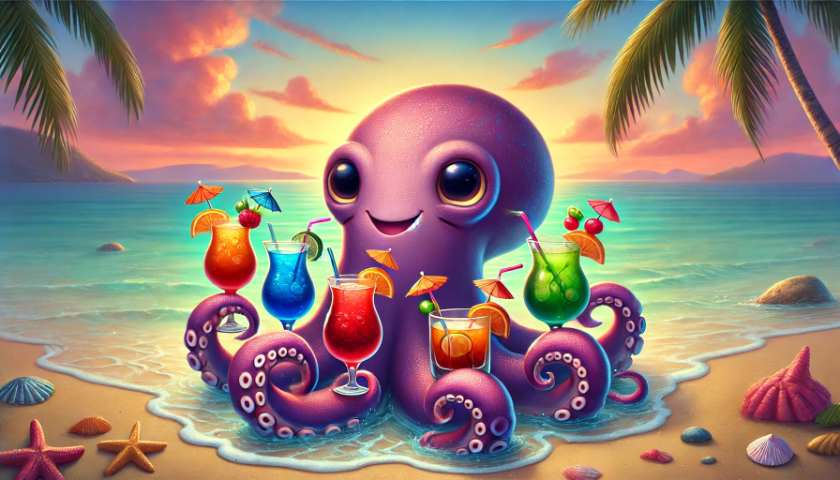
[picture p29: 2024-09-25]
Programmierung/AS/Logical/mappView/Resources/Media/Bilder/Kraken_smile.png

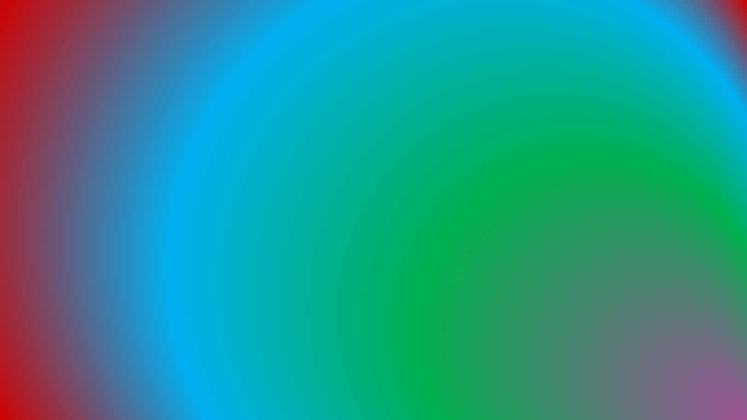
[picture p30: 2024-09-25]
Programmierung/AS/Logical/mappView/Resources/Media/Bilder/gradient.png

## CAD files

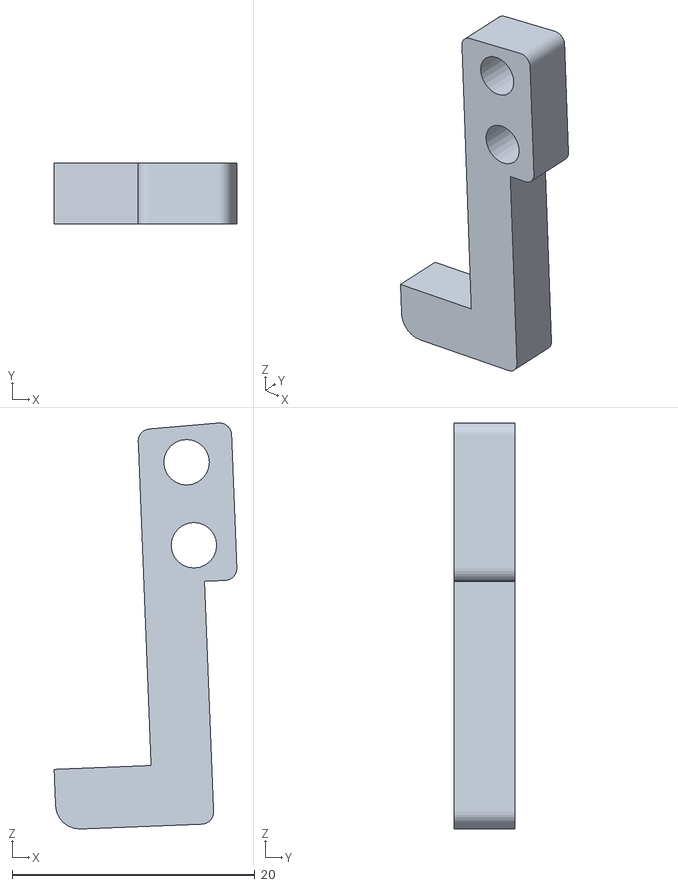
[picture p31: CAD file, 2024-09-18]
3D-Modelle/3D-Modelle/Ausschankarm/Schwammhalter.stl
15.1 x 5.00 x 33.5

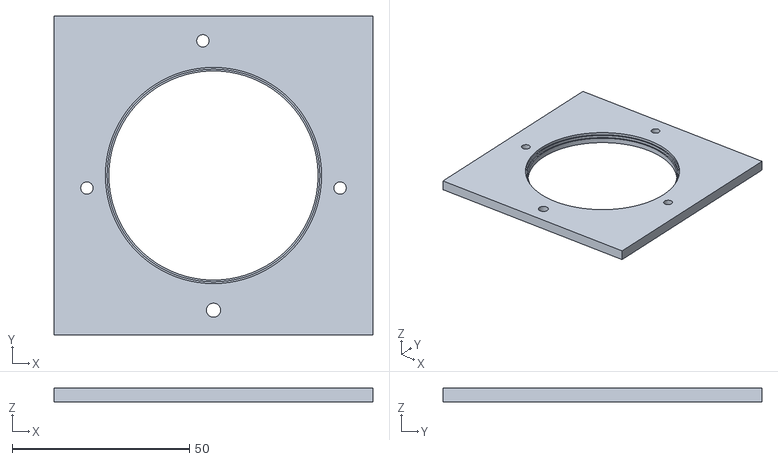
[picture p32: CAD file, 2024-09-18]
3D-Modelle/3D-Modelle/Becherhalter/Abschlussplatte.stl
90.0 x 90.0 x 4.00

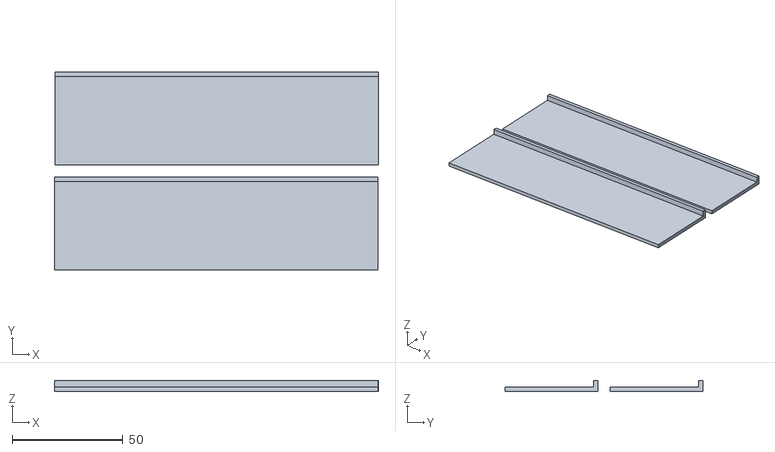
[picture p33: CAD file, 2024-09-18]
3D-Modelle/3D-Modelle/Becherspender/Manschette Rohr Dichtung v1.stl
146.3 x 89.5 x 5.00

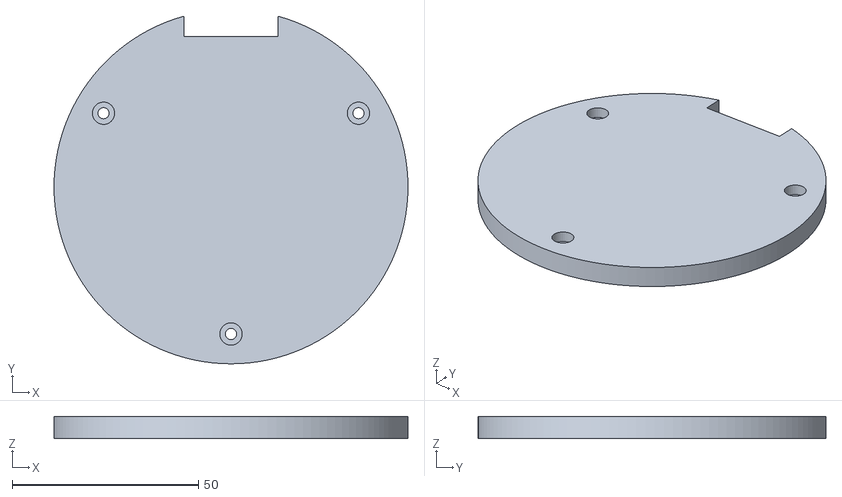
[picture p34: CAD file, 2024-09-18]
3D-Modelle/3D-Modelle/Becherspenderbeleuchtung/Deckel Gesamtgehäuse.stl
95.0 x 93.3 x 6.00

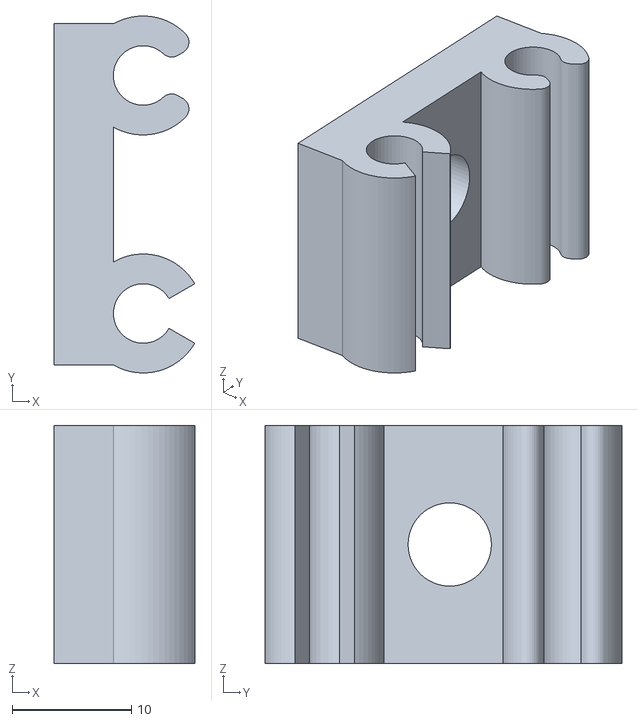
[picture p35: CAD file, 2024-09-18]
3D-Modelle/3D-Modelle/Befestigungen/Schlauchhalter/Schlauchhalterung einzeln v2.stl
11.8 x 30.0 x 20.0

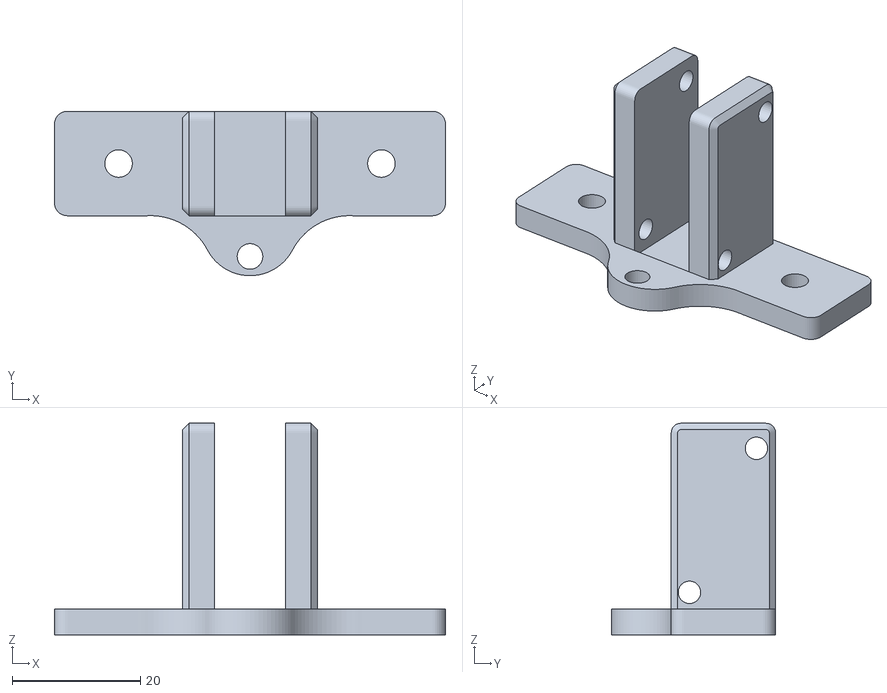
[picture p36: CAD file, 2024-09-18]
3D-Modelle/3D-Modelle/Befestigungen/Sensorhalterung v8.stl
61.0 x 25.6 x 33.0

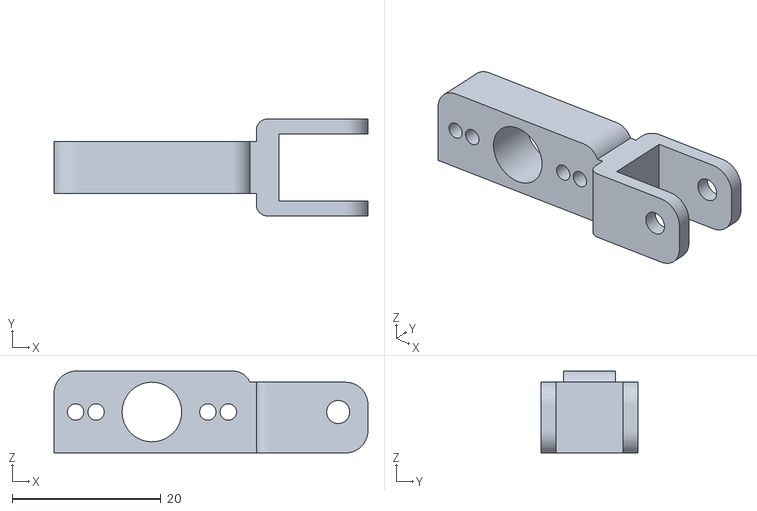
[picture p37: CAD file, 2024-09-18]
3D-Modelle/3D-Modelle/Eisspender/Auslösmechanismus/Servoarmadapter.stl
42.2 x 13.0 x 11.0

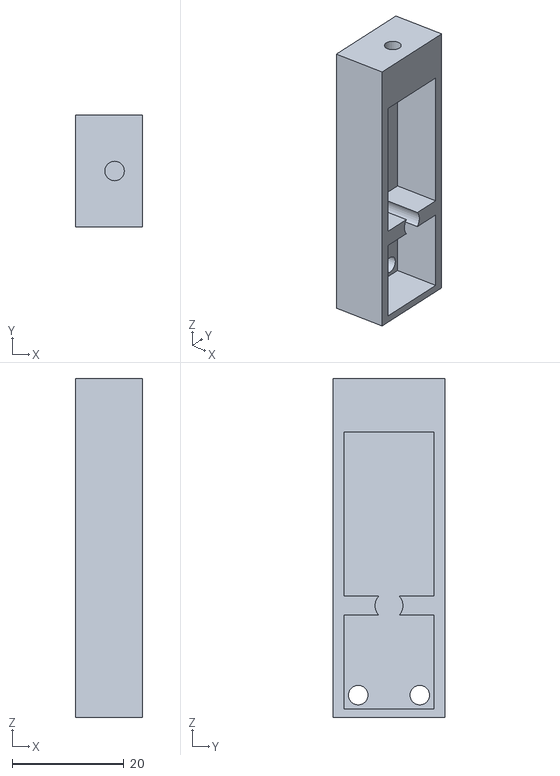
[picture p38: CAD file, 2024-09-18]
3D-Modelle/3D-Modelle/Eisspender/Lichtschranke/Fotozellenhalterung.stl
12.0 x 20.0 x 60.6

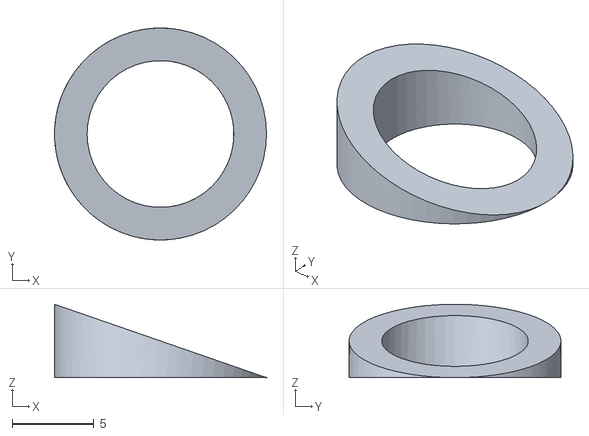
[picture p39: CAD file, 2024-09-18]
3D-Modelle/3D-Modelle/Eisspender/Rutschenhalterung/Unterlegscheibe-schräg.stl
13.0 x 13.0 x 4.50

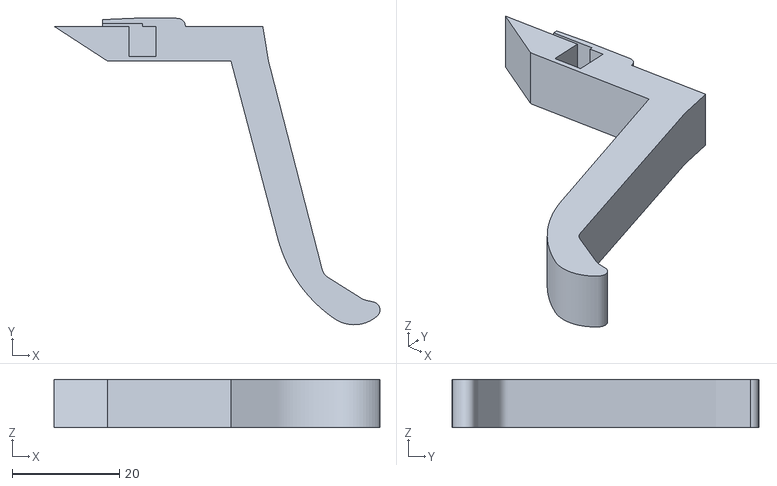
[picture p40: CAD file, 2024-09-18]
3D-Modelle/3D-Modelle/Endlagenschalter/Endlagenschalter_Armverlängerung_Becherspender.stl
60.8 x 57.1 x 9.00

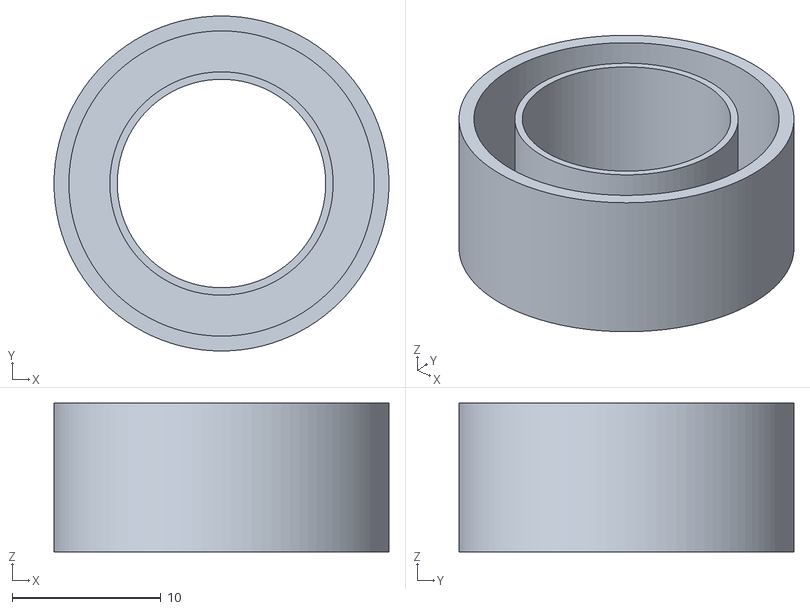
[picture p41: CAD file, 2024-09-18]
3D-Modelle/3D-Modelle/Versorgung/Alurohrendkappe.stl
22.5 x 22.5 x 10.0

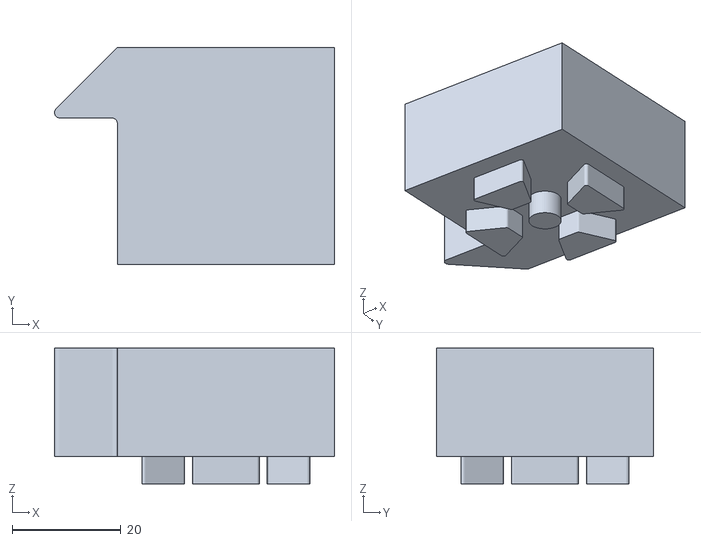
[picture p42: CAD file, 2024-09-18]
3D-Modelle/3D-Modelle/Winkelabdeckkappen/Abschlusskappe 40x40 Special Fernseher v2.stl
51.6 x 40.0 x 25.0

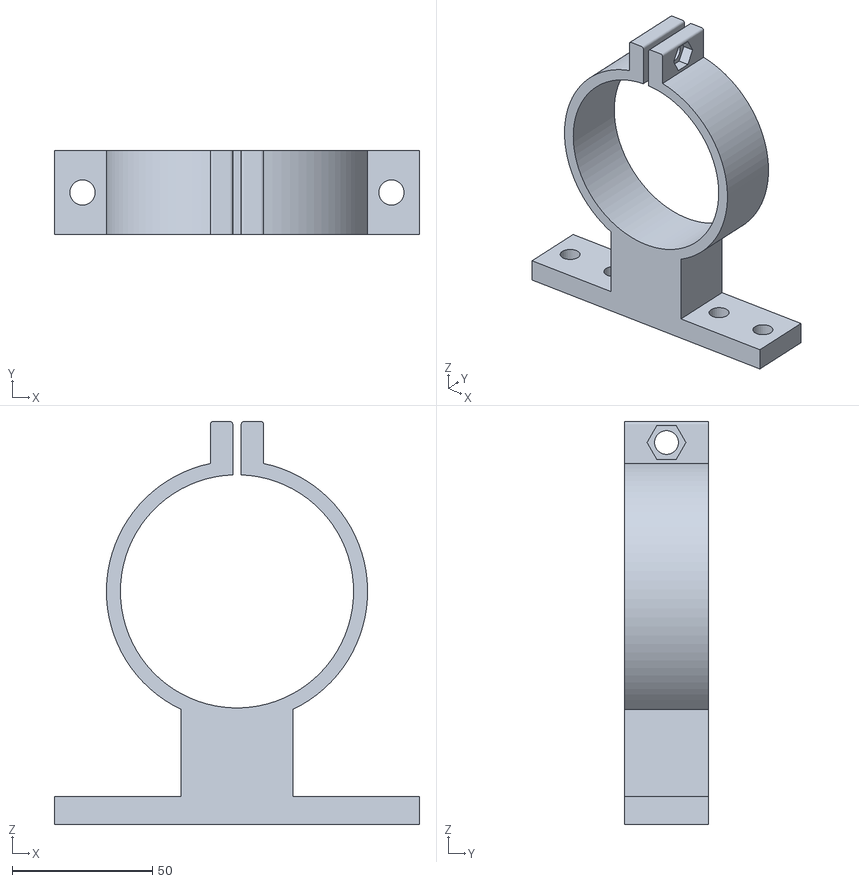
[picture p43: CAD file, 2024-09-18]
3D-Modelle/3D-Modelle/Zitronenspender/Zitrone_RohrHalterung.stl
130.0 x 30.0 x 143.5

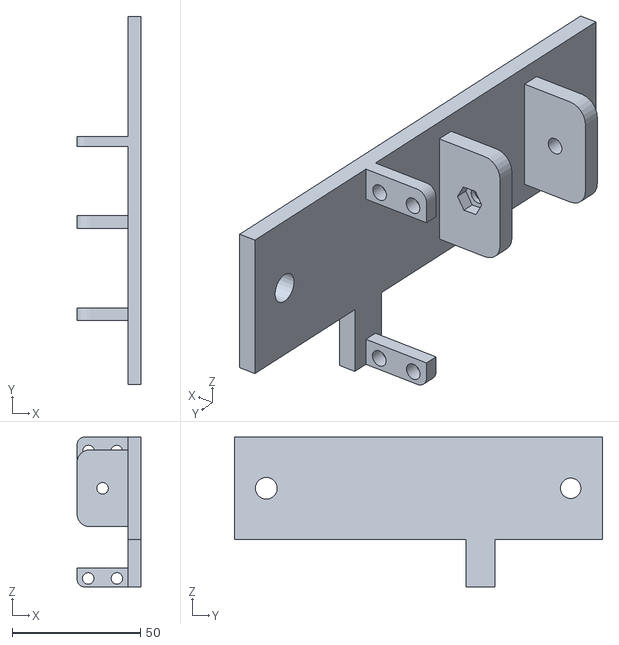
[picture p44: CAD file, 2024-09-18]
3D-Modelle/3D-Modelle/Ausschankarm/Befestigungsplatte.stl
25.0 x 143.7 x 58.5

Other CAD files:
3D-Modelle/3D-Modelle/Becherhalter/Abstandsleiste.stl
3D-Modelle/3D-Modelle/Becherspender/Endkappe oben v5.stl
3D-Modelle/3D-Modelle/Becherspenderbeleuchtung/Halterung LED Unten.stl
3D-Modelle/3D-Modelle/Befestigungen/ESP Halterung v2.stl
3D-Modelle/3D-Modelle/Ausschankarm/Arm.stl
3D-Modelle/3D-Modelle/Ausschankarm/Ausschankkopf.stl
3D-Modelle/3D-Modelle/Ausschankarm/Zugentlastung.stl
3D-Modelle/3D-Modelle/Becherhalter/Bodenplatte.stl
3D-Modelle/3D-Modelle/Becherhalter/Federhalterung.stl
3D-Modelle/3D-Modelle/Becherhalter/Gehäuse.stl
3D-Modelle/3D-Modelle/Becherhalter/große Fangkorbhälfte.stl
3D-Modelle/3D-Modelle/Becherhalter/kleine Fangkorbhälfte.stl
3D-Modelle/3D-Modelle/Becherspender/Endkappe unten v2.stl
3D-Modelle/3D-Modelle/Becherspender/Greifarm V3 v4.stl
3D-Modelle/3D-Modelle/Becherspender/Manschette Rohr v1.stl
3D-Modelle/3D-Modelle/Becherspender/Servo Halterung v2.stl
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

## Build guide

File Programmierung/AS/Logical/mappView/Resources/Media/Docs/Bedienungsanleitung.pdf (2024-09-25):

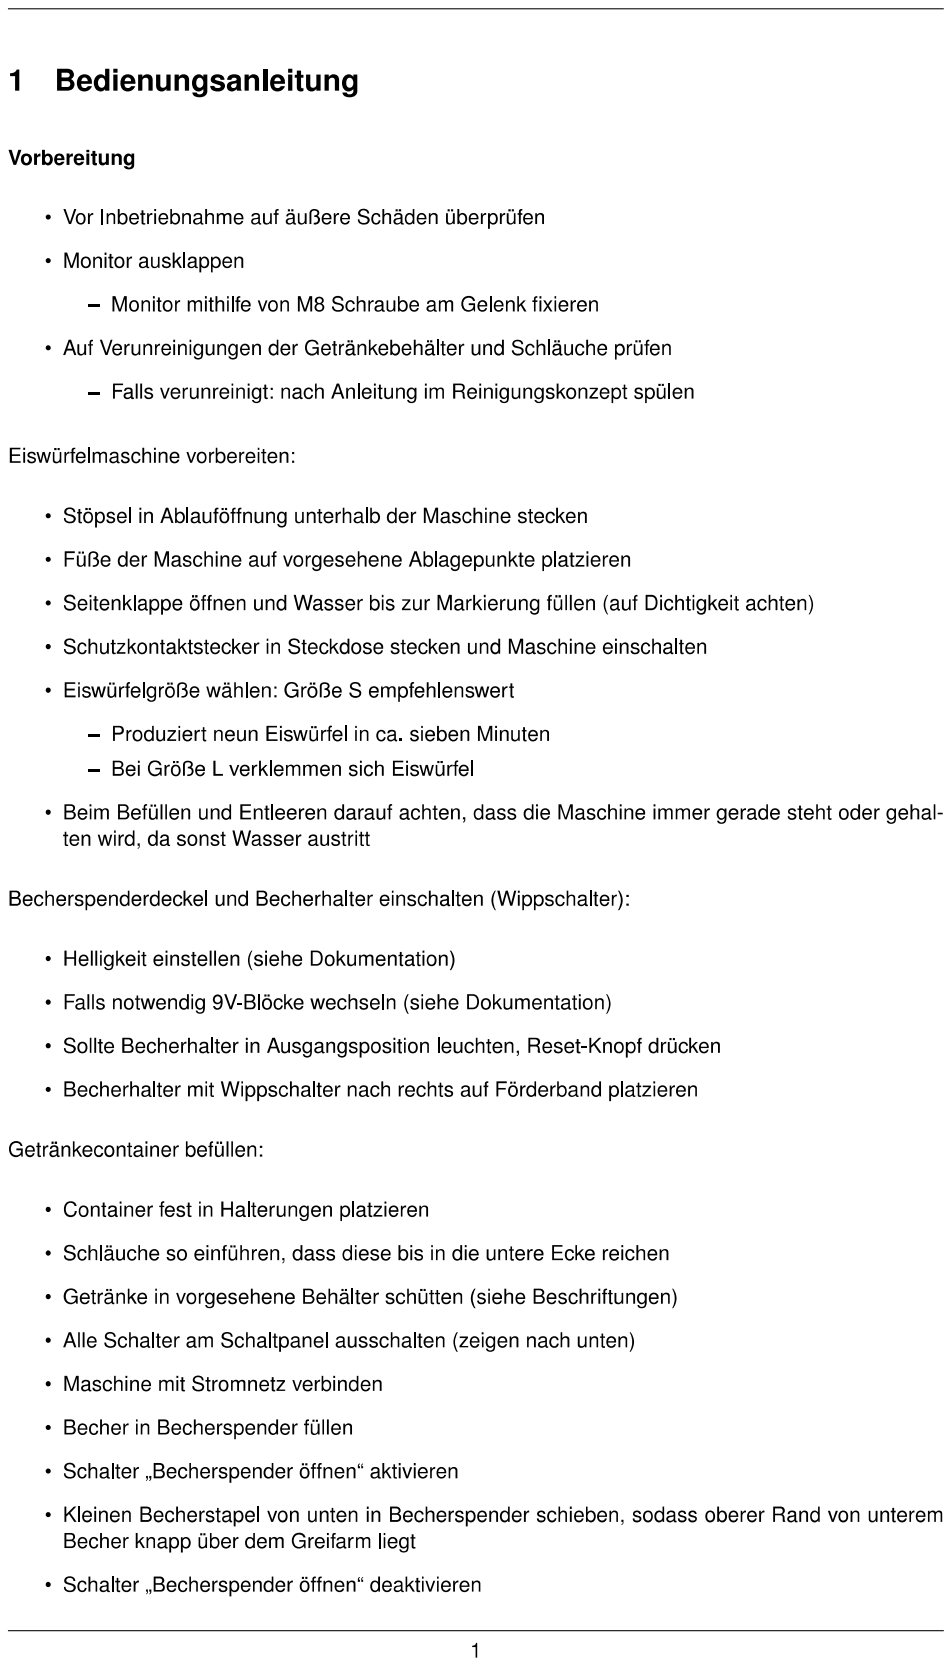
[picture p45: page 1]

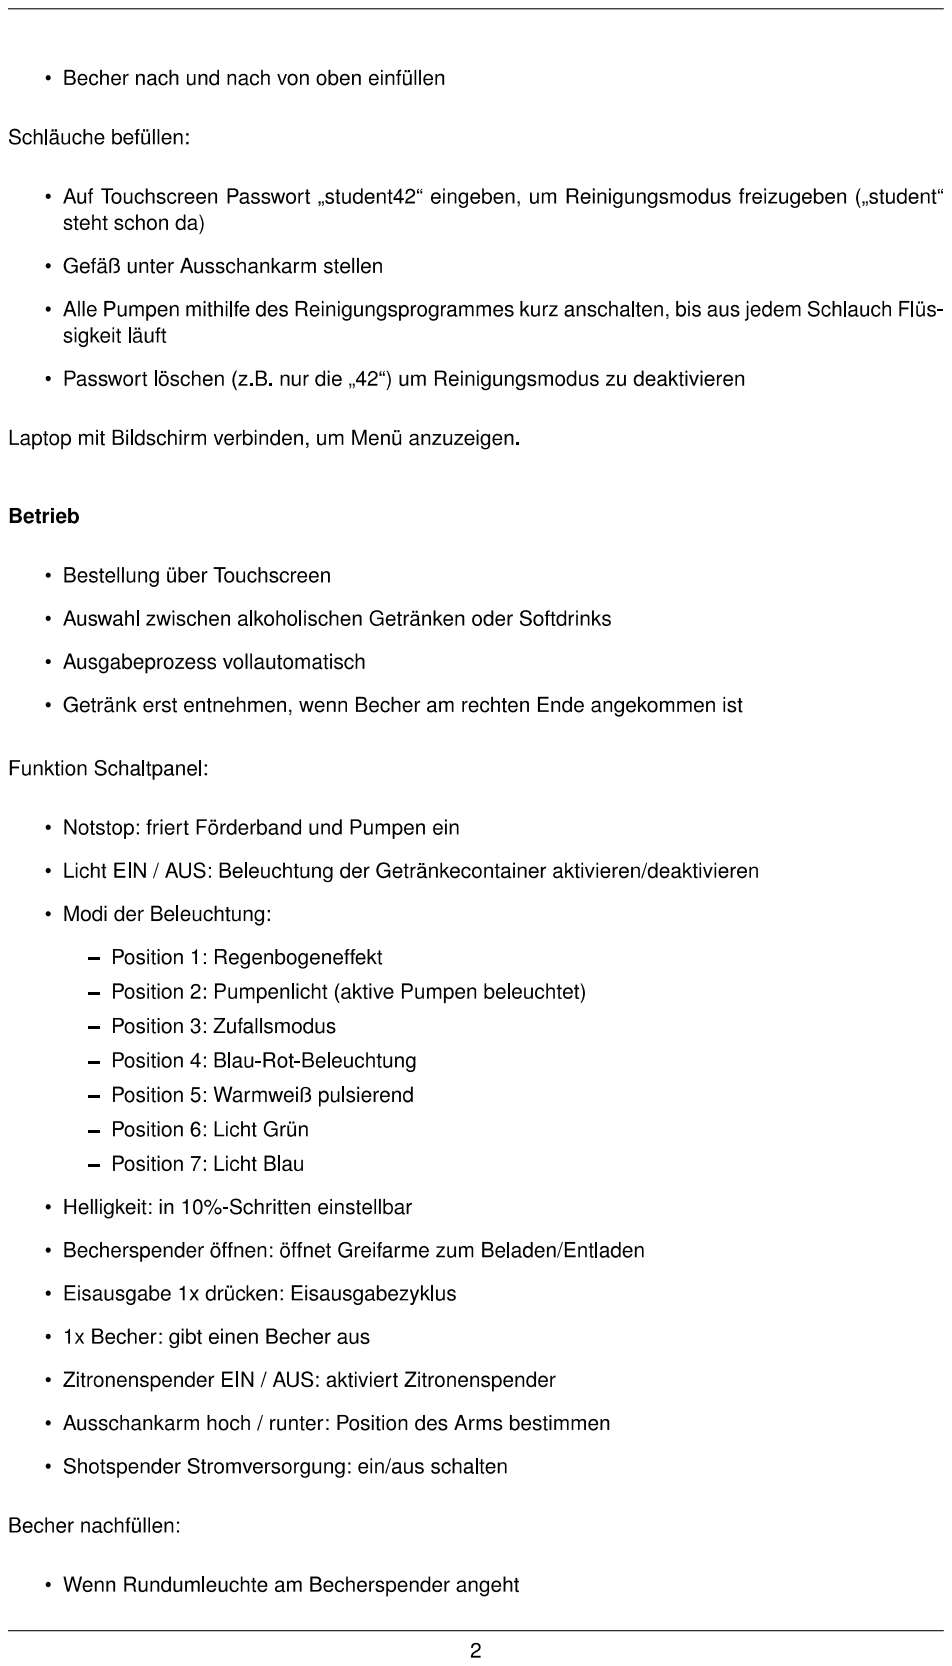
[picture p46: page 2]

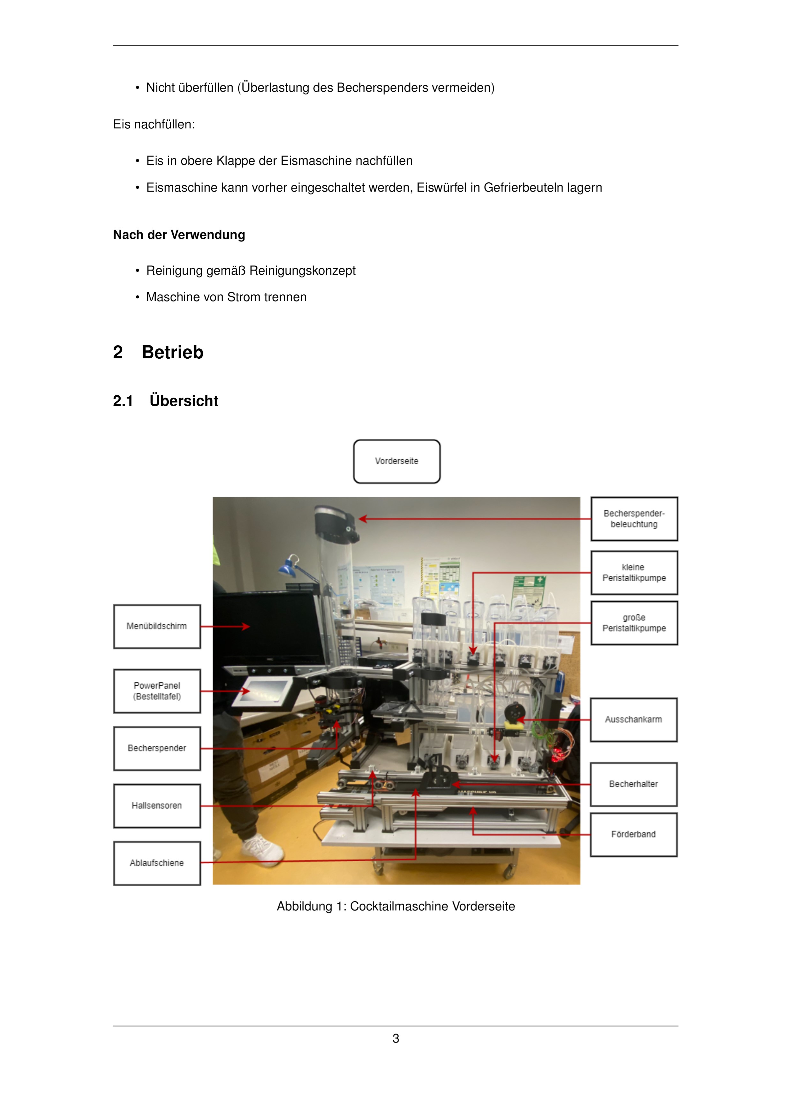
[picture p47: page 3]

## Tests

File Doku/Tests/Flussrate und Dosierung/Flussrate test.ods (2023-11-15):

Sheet: Flussrate_P1
Menge / g | Zeit / s
10 | 5.2
20 | 4.6
30 | 4.94
40 | 5.26
50 | 4.64
60 | 4.84
70 | 5.09
80 | 4.63
90 | 5.25
100 | 4.66
110 | 4.87
120 | 4.46
 |  | 4.87 | s / 10 g
 |  | 0.487 | /1s

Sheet: Rezepte_Cocktails
Name | Zutat 1 | Zutat 2 | Zutat 3 | Zutat 4 | Zutat 5?
Cuba Libre | Rum | Cola | Limetten
Blue Lady | Gin | Blue Curacao | Zitronensaft
Gin Tonic | Gin | Tonic | Zitronen
Screwdriver (Wodka-O) | Wodka | Osaft
Wodka Lemon | Wodka | Limettensaft | Bitterlemon | Limette
Wodka Energy | Wodka | Energy Drink
Cape Cod | Wodka | Limettensaft | Cranberrysaft | Limette
Tequila Sunrise | Tequila | Osaft | Grenadine
Bee's Knees | Gin | Zitronensaft | Honigsirup | Osaft
Daiquiri | Rum | Limettensaft | Zuckersirup
Long Island Iced Tea | Rum | Wodka | Gin | Tequila | Cointreau | Limettensaft | Cola | Limette
Planters Punch | Rum | Osaft | Zitronensaft | Grenadine | Zuckersirup | Zitrone
Blue Lagoon | Ananassaft | Rum | Blue Curacao | Ananas
Angel Blue | Wodka | Blue Curacao | Zitronenlimo | Zitrone
High Voltage | Zitronensaft | Wodka | Blue Curacao | Gin Tonic

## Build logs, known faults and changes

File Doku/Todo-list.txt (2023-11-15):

Todo-List:
Pumpenkauf ok
Pumpentest ok
Dokumentation
Reinigungskonzept
...

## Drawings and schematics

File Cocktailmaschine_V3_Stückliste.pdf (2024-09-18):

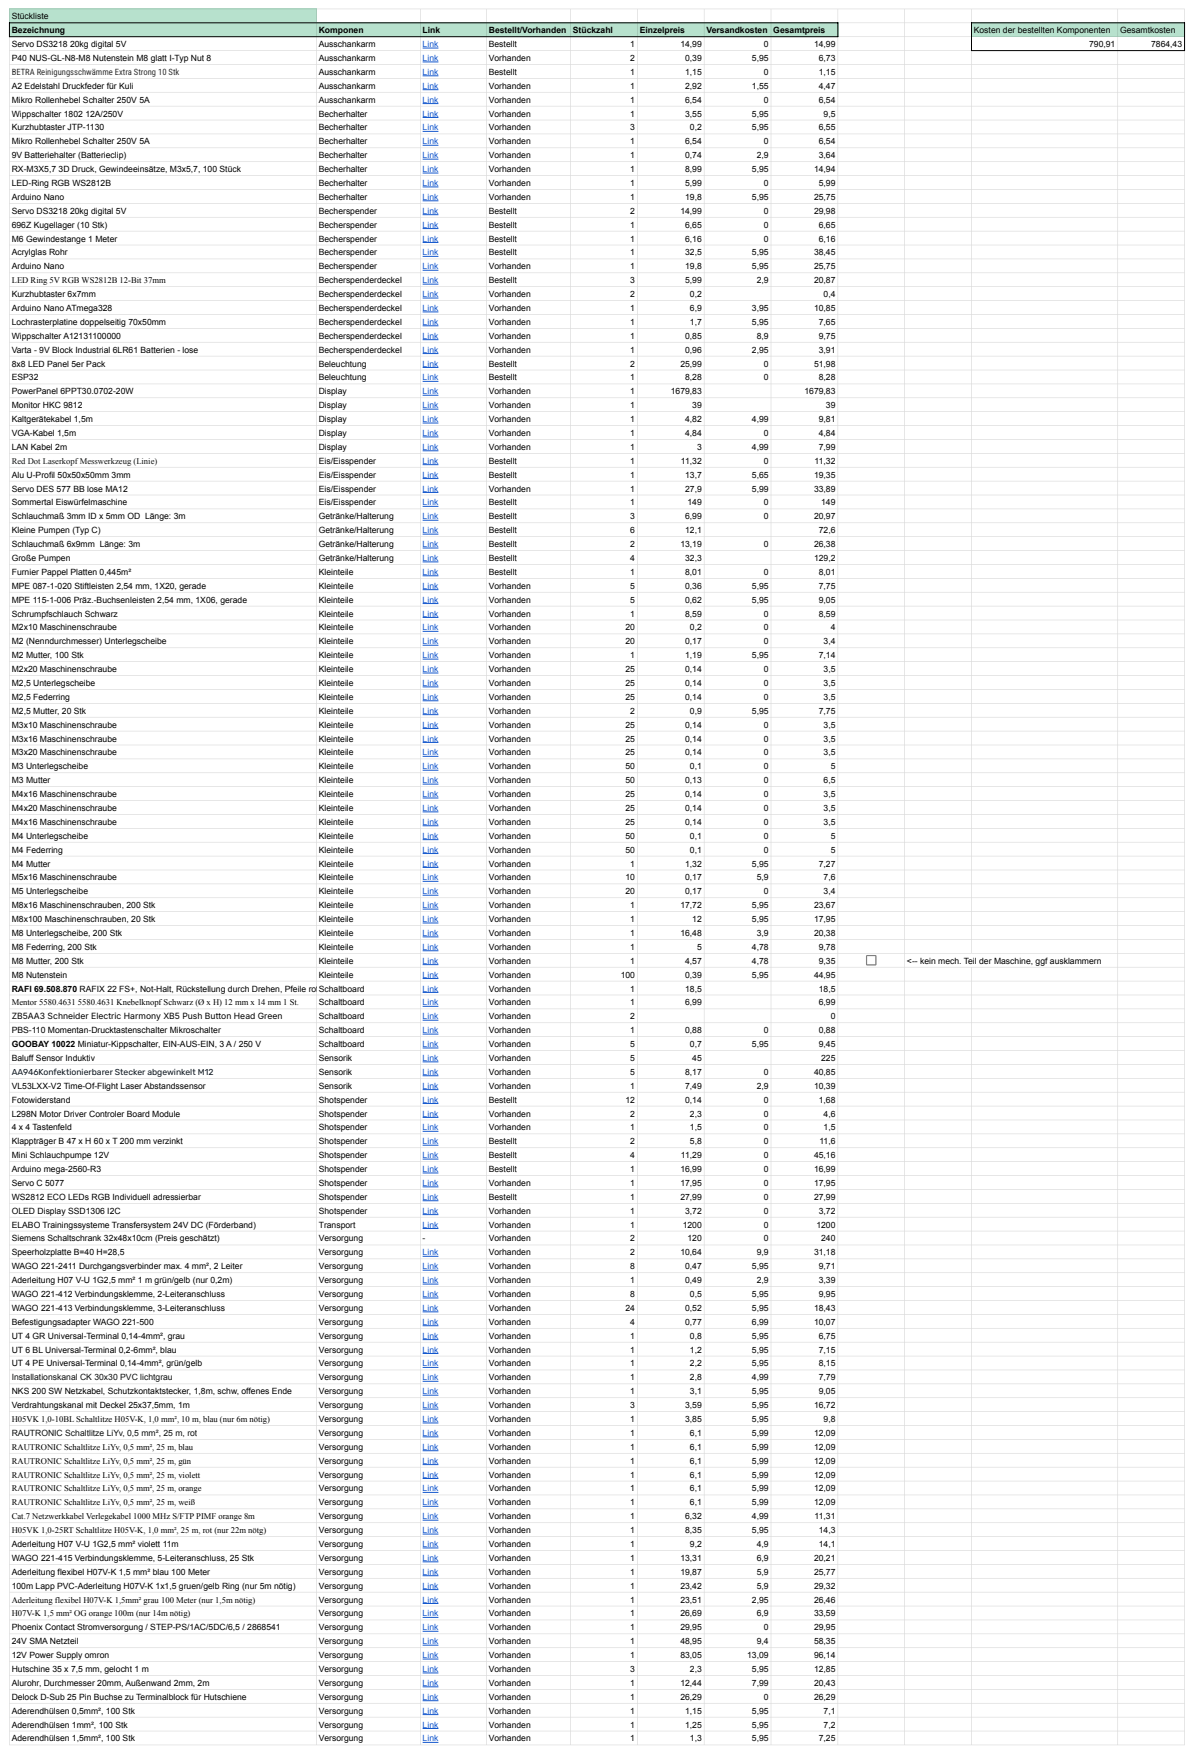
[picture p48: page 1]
Stückliste Bezeichnung; Komponen; Link; Bestellt/Vorhanden Stückzahl; Einzelpreis; Versandkosten Gesamtpreis; Kosten der bestellten Komponenten Gesamtkosten Servo DS3218 20kg digital 5V; Ausschankarm; Bestellt; 7864,43 P40 NUS-GL-N8-M8 Nutenstein M8 glatt I-Typ Nut 8; Vorhanden; BETRA Reinigungsschwämme Extra Strong 10 Stk; 1,15 A2 Edelstahl Druckfeder für Kuli; 4,47 Mikro Rollenhebel Schalter 250V 5A; 6,54 Wippschalter 1802 12A/250V; Becherhalter; 9,5 Kurzhubtaster JTP-1130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

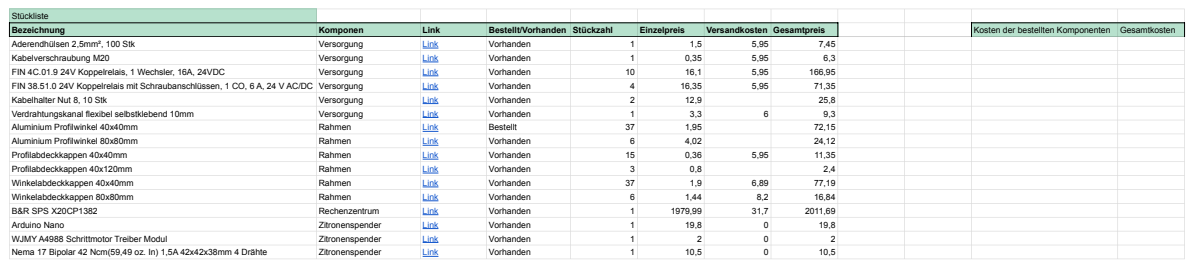
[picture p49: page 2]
Stückliste Bezeichnung; Komponen; Link; Bestellt/Vorhanden; Stückzahl; Einzelpreis; Versandkosten; Gesamtpreis; Kosten der bestellten Komponenten; Gesamtkosten Aderendhülsen 2,5mm², 100 Stk; Versorgung; Vorhanden; 7,45 Kabelverschraubung M20; 6,3 FIN 4C.01.9 24V Koppelrelais, 1 Wechsler, 16A, 24VDC; 166,95 FIN 38.51.0 24V Koppelrelais mit Schraubanschlüssen, 1 CO, 6 A, 24 V AC/DC Versorgung; 71,35 Kabelhalter Nut 8, 10 Stk; 25,8 Verdrahtungskanal flexibel selbstklebend 10mm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

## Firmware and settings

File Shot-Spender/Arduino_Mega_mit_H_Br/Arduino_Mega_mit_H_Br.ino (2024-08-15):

#include <Adafruit_SSD1306.h>
#include <Adafruit_GFX.h>
#include <Adafruit_NeoPixel.h>
#include <Servo.h>
#include <Keypad.h>

// Keypad-Konfiguration
const byte COLS = 4;
const byte ROWS = 4;
char hexaKeys[ROWS][COLS] = {
  {'D', '#', '0', '*'},
  {'C', '9', '8', '7'},
  {'B', '6', '5', '4'},
  {'A', '3', '2', '1'}
};
byte colPins[COLS] = {2, 3, 4, 5};
byte rowPins[ROWS] = {6, 7, 8, 9};
char Taste;
Keypad Tastenfeld = Keypad(makeKeymap(hexaKeys), rowPins, colPins, ROWS, COLS);

// OLED-Display-Konfiguration
#define OLED_RESET -1
#define SCREEN_HEIGHT 32
#define SCREEN_WIDTH 128
Adafruit_SSD1306 display(SCREEN_WIDTH, SCREEN_HEIGHT, &Wire, OLED_RESET);

// Pin-Definitionen
#define CALIBRATE_BUTTON_PIN 11 
#define NUM_BECHERS 6
#define NUM_PUMPS 4
#define SERVO_PIN 12 
#define NEOPIXEL_PIN 10 
#define NUM_LEDS 24

// Pins für Lichtsensoren
#define LIGHT_SENSOR1_PIN A0
#define LIGHT_SENSOR2_PIN A1
#define LIGHT_SENSOR3_PIN A2
#define LIGHT_SENSOR4_PIN A3
#define LIGHT_SENSOR5_PIN A4
#define LIGHT_SENSOR6_PIN A5

// Pins für Pumpensteuerung
#define PUMP1_DIR_PIN 26
#define PUMP1_PWM_PIN 27
#define PUMP2_DIR_PIN 28
#define PUMP2_PWM_PIN 29
#define PUMP3_DIR_PIN 30
#define PUMP3_PWM_PIN 31
#define PUMP4_DIR_PIN 32
#define PUMP4_PWM_PIN 33

#define PUMP_TIME 300
#define PUMP_REVERSE_TIME 100

// Globale Variablen
int selectedBechers = 0;
int selectedPump = 0;
Servo pumpServo;
Adafruit_NeoPixel strip = Adafruit_NeoPixel(NUM_LEDS, NEOPIXEL_PIN, NEO_GRB + NEO_KHZ800);
int lightThreshold = 500;

void setup() {
  Serial.begin(115200);

  pinMode(CALIBRATE_BUTTON_PIN, INPUT_PULLUP);

  for (int i = 0; i < NUM_PUMPS; i++) {
    pinMode(PUMP1_DIR_PIN + i * 2, OUTPUT);
    pinMode(PUMP1_PWM_PIN + i * 2, OUTPUT);
    digitalWrite(PUMP1_DIR_PIN + i * 2, LOW);
    analogWrite(PUMP1_PWM_PIN + i * 2, 0);
  }

  if(!display.begin(SSD1306_SWITCHCAPVCC, 0x3C)) {
    Serial.println(F("SSD1306 allocation failed"));
    for(;;);
  }
  // Display Initialisierung zusammenhalten
  display.display(); // braucht es das
  delay(2000); // braucht es das
  display.clearDisplay(); 
  display.display(); //Braucht es das?

  pumpServo.attach(SERVO_PIN);

  // LED Strip
  strip.begin();
  strip.show();

  updateDisplay();
}

void loop() {
  Taste = Tastenfeld.getKey();
  if (Taste) {
    handleKeypadInput(Taste);
  }

  if (digitalRead(CALIBRATE_BUTTON_PIN) == LOW) {
    calibrateSensors();
    delay(1000);
  }

  checkBechers();
  
  if (allBechersPresent()) {
    fillBechers();
  }
}

// Verarbeitung der Tastatureingaben
void handleKeypadInput(char key) {
  switch (key) {
    // Anzahl der Becher
    case '1': case '2': case '3': case '4': // Zu wenig cases
      selectedBechers = key - '0';
      updateDisplay();
      delay(300);
      break;
    
    // Likör sorte
    case 'A': case 'B': case 'C': case 'D':
      selectedPump = key - 'A' + 1;
      updateDisplay();
      delay(300);
      break;
  }
}

// Aktualisierung des Displays
void updateDisplay() {
  display.clearDisplay(); // Bildschirm löschen
  display.setTextSize(5); // Textgröße für die Becheranzahl setzen
  display.setTextColor(WHITE); // Textfarbe auf Weiß setzen

  // Becheranzahl anzeigen
  display.setCursor(0, 0); // Cursor auf obere linke Ecke setzen
  display.print(selectedBechers); // Anzahl der ausgewählten Becher drucken

  // Pumpennummer anzeigen
  display.setTextSize(3); // Textgröße für die Pumpennummer setzen
  display.setCursor(0, 25); // Cursor auf eine neue Zeile setzen
  display.print((char)('A' + selectedPump - 1)); // Buchstabe der ausgewählten Pumpe drucken

  display.display(); // Display aktualisieren
}

// Überprüfung der Becher
void checkBechers() {
  int becherCount = 0;
  for (int i = 0; i < NUM_BECHERS; i++) {
    int sensorValue = analogRead(LIGHT_SENSOR1_PIN + i);
    if (sensorValue < lightThreshold) {
      becherCount++;
      setHolderColor(i, 0, 255, 0);
    } else {
      setHolderColor(i, 255, 0, 0);
    }
  }
  strip.show();
}

// Überprüfung, ob alle Becher vorhanden sind
bool allBechersPresent() {
  int becherCount = 0;
  for (int i = 0; i < NUM_BECHERS; i++) {
    if (analogRead(LIGHT_SENSOR1_PIN + i) < lightThreshold) {
      becherCount++;
    }
  }
  return (becherCount == selectedBechers);
}

// Aktivierung der Pumpe
void activatePump(int pump, bool reverse = false) {
  int dirPin = PUMP1_DIR_PIN + (pump - 1) * 2;
  int pwmPin = PUMP1_PWM_PIN + (pump - 1) * 2;
  digitalWrite(dirPin, reverse ? LOW : HIGH);
  analogWrite(pwmPin, 255);
}

// Deaktivierung der Pumpe
void deactivatePump(int pump) {
  int pwmPin = PUMP1_PWM_PIN + (pump - 1) * 2;
  analogWrite(pwmPin, 0);
}

// Füllen der Becher
void fillBechers() {
  if (selectedBechers > 0 && selectedPump > 0) {
    int angleStep = 180 / NUM_BECHERS;
    for (int i = 0; i < selectedBechers; i++) {
      pumpServo.write(i * angleStep);
      delay(500);
      activatePump(selectedPump);
      delay(PUMP_TIME);
      deactivatePump(selectedPump);
      activatePump(selectedPump, true);
      delay(PUMP_REVERSE_TIME);
      deactivatePump(selectedPump);
      delay(500);
    }
  }
}

// Einstellung der LED-Farbe für die Halterung
void setHolderColor(int holderIndex, uint8_t red, uint8_t green, uint8_t blue) {
  int ledIndex = holderIndex * 4;
  for (int i = 0; i < 4; i++) {
    strip.setPixelColor(ledIndex + i, strip.Color(red, green, blue));
  }
}

// Kalibrierung der Sensoren
void calibrateSensors() {
  Serial.println("Kalibriere Sensoren...");
  int maxSensorvalue = 0;
  for (int i = 0; i < NUM_BECHERS; i++) {
    int sensorValue = analogRead(LIGHT_SENSOR1_PIN + i);
    if (sensorValue > maxSensorvalue) {
      maxSensorvalue = sensorValue;
    }
    Serial.print("Sensor ");
    Serial.print(i);
    Serial.print(" - Wert: ");
    Serial.println(sensorValue);
    delay(500);
  }
  lightThreshold = maxSensorvalue - 10;
  Serial.println("Kalibrierung abgeschlossen.");
  Serial.print("Neuer Schwellenwert: ");
  Serial.println(lightThreshold);
}

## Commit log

2023-11-15 Hinzufuegen von Grundstruktur
    [Flussrate test.ods]
2023-12-21 Kleine Änderung an der readme datei
2023-12-21 Anpassung der Regeln
2024-01-11 Induktiver Sensor Test Schlauchpumpentest1
2024-04-04 grundstruktur switch case
2024-05-07 Seite hinzugefügt für Wartebalken Funktionierender Durchlauf des Fließbandes Bestellen möglich --> noch nicht perfekt
2024-05-13 Hinzufügen von Arduino Stationen, Endlageschaltern
2024-05-16 Hinzufügen von Funktionen (Notstopknopf, resetToStart, Cocktailanpassung und änderung) -bich -gentleben +gintonic
2024-05-16 Cocktail gelöscht und neue eingefügt --> Testcocktail; Analogpins auf Digitalpins umgestellt
2024-05-16 Visualisierung mit knöpfen, die sich zurücksetzen
2024-05-21 Viusaliserung angepasst und einfügen einer Pause
2024-05-21 Stable Version für Fakultätsfest, Pause nach Becherentnahme eingefügt und Blue Lagoon in Visualisierung eingefügt
2024-05-21 Website Binding --> Springt wieder auf den Start zurück nach durchlauf
2024-08-12 Lichtschranke eingebunden durch Arduino
2024-08-14 Switch Case für Cocktailablauf noch unfertig
2024-08-15 Arm fertig einprogrammiert
2024-08-15 Becherausgabe in Switch-Case umgewandelt
2024-08-15 Becherausgabe ist unabhängig von dem Reed Sensor. Dieser Springt im Notfall weiterhin ein
2024-08-15 Reinigungsprogramm-> Es wird erst nach rechts und danach nach links gefahren --> Damit die erste Station nicht ausgelassen wird.
2024-09-18 Hinzufügen der 3D-Modelle
    [6er Schlauchhalterung v3.stl, Abschlusskappe 40x40 Special Fernseher v2.stl, Abschlusskappe Alu-Profil 40x40 v2.stl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]
2024-09-25 Änderungen an der Visualierung
2024-09-25 Einfügen von Bildern für alle sichtbaren Seiten und verschieben des Testcocktails in das Reinigungsprogramm
2024-09-25 Einfügen eines Knopfes zum starten und stoppen aller Pumpen gleichzeitig
